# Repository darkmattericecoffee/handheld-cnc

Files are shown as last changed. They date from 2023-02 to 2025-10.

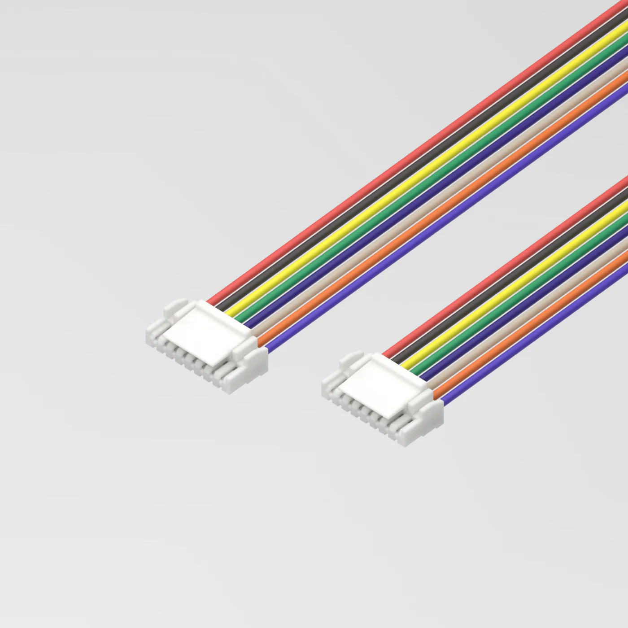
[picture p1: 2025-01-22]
cad/cha/sensor_ETH_20_CAT5/resources/jst_gh_8pin_v2.webp

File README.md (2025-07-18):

## Description
Compass is a DIY handheld CNC router designed to make CNC machining more accessible.

v1

Unlike traditional CNC machines that move a cutting tool within a fixed workspace, Compass relies on users to guide the device around the workpiece directly. It automatically adjusts the cutting tool to stay on the programmed design path, enabling a significantly smaller device footprint while still handling large-scale cuts.

This is all accomplished using optical flow mouse sensors to track the position of the device, as well as a lead screw driven gantry to adjust the tool. The brains are a Teensy 4.1 microcontroller.

## Getting Started
This repo contains all of the source to build a Handheld CNC Router: the firmware, CAD files for 3D printing/manufacturing, BOM, and cable diagrams.

### Navigation
Internal
- [main](main/) - main firmware (written for [PlatformIO](https://docs.platformio.org/en/latest/core/quickstart.html) usage)
- [cad](cad/) - custom hardware (3D prints, laser cut sheet metal, cable harnesses)
- [pcb](pcb/) - printed circuit board designs for motherboard and sensors
- [dev](dev/) - development folder for debugging and testing

External
- [BOM](https://docs.google.com/spreadsheets/d/12QS1CGSAB-lqKIOotCXDaXmJv9cjfRvVEAgQbRd7MnY/edit?usp=sharing)
- [Assembly Instructions](https://drive.google.com/drive/folders/1fIALrTWUbJRqTl93RGrUaR8dMfO7AI_g?usp=sharing)

## Disclaimer
This project is a work-in-progress. Development is rapidly occurring, so design files and firmware may change.

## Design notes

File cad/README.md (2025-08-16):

# Manufacturing BOM
Print all parts at 40% infill or higher. 

## 3D Printed Parts (PLA, unless stated otherwise)
- (2x) baseStage.stl
- (1x) baseStagePlug.stl
- (2x) cableClip.stl
- (1x) displayRing.stl
	- *_ae* if using AliExpress display
	- *_ws* if using Amazon Waveshare display
- (1x) frameUILeft.stl
- (1x) frameUIRight.stl
- (2x) handle.stl
- (1x) idlerMountLeft.stl
- (1x) idlerMountRight.stl
- (1x) mainFrame.stl
- (1x) motherEnclosure.stl
- (4x) PMW3360-sled.stl *(print at 0.1mm or 0.2mm layer height)*
- (1x) shieldSeperator.stl
- (3x) spacer_enclosure.stl
- (4x) springMount.stl *(print at 0.1mm or 0.2mm layer height)*
- (1x) stepperMountLeft.stl
- (1x) stepperMountRight.stl
- (1x) stepperMountZ.stl
- (2x) tensionPlug.stl
- (1x) vacMount.stl
- (1x) xStagePlate.stl
- (1x) yStagePlate.stl
- (1x) zCarriage.stl
- (1x) zKnob.stl
### Tool Mounts (PLA)
- 65mm tool mount (Makita RT0701C or any Makita router clone)
	- (2x) routerMount_65.stl
- 69mm tool mount (DeWalt 611) - *untested*
	- (2x) routerMount_69.stl
- Pen mounts (for testing)
	- (1x) penMount_65.stl
	- (1x) penMount_pm-65.stl
		- pen mount made for a Paper Mate flair tip pen
		- also randomly works for a Uniball rollerball
	- (1x) penMount_flange-pm-65.stl
		- same as above, but with a flange for easier alignment
### Jigs (PLA)
- (1x) encoderJig.stl
- (1x) beltShim.stl
- (1x) sensorJig.stl

## Aluminum Sheet Metal (6061)
- (1x) basePlate.dxf - 6mm (1/4" also works)
- (1x) facePlate.dxf - 1/16"
	- Note: this can be made in wood or acrylic too (1/8" should be fine) since it's not structural.
	- It can also be 3D printed or made using a PCB (see PCB folder...)

## Cable Harnesses
- (2x) sensorWire_ETH_20_CAT5
- (2x) sensorWire_ETH_40_CAT5

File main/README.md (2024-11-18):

## Debugging
To produce a debug logFile to use with `debugViewer.ipynb`, make sure the variable `outputMode` in your firmware is set to `1`. Then run the following code in a *platformIO terminal*:
```
pio device monitor > /logFiles/logFile_XX.txt
```

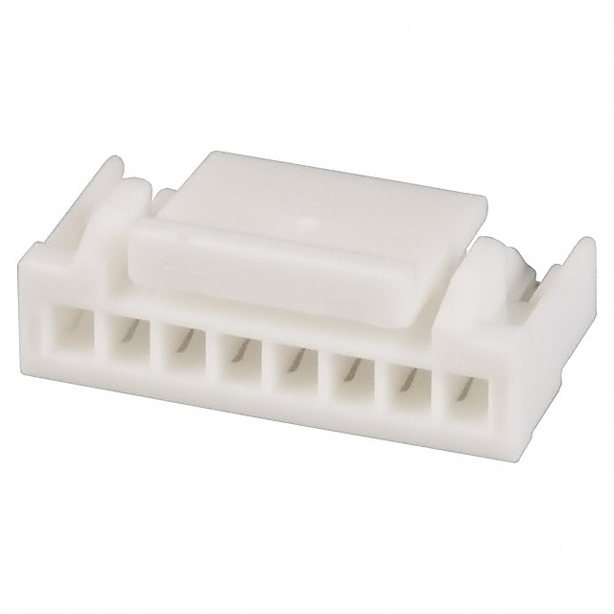
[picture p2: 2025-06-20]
cad/cha/sensor_ETH_20_CAT5/resources/GH-8.jpg

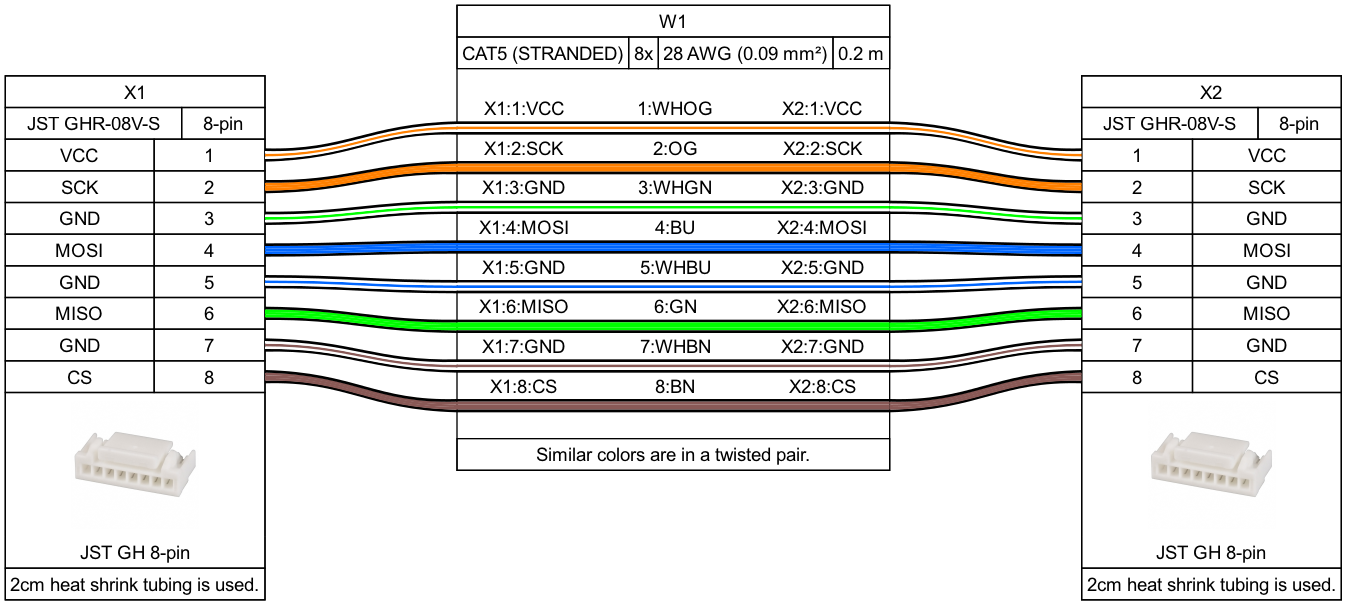
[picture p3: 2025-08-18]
cad/cha/sensor_ETH_20_CAT5/sensor_ETH_20_CAT5.png

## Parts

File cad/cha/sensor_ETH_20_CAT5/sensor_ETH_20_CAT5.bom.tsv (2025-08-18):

Id | Description | Qty | Unit | Designators
1 | Cable, CAT5 (STRANDED), 8 x 28 AWG | 0.2 | m | W1
2 | Connector, JST GHR-08V-S, 8 pins | 2 |  | X1, X2

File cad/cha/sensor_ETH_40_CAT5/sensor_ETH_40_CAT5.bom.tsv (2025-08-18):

Id | Description | Qty | Unit | Designators
1 | Cable, CAT5 (STRANDED), 8 x 28 AWG | 0.4 | m | W1
2 | Connector, JST GHR-08V-S, 8 pins | 2 |  | X1, X2

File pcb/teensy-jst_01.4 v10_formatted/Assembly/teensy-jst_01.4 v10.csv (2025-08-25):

Qty | Value | Device | Package | Parts | Description | AVAILABILITY | CATEGORY | CHECK_PRICES | COPYRIGHT | DESCRIPTION | MANUFACTURER | MANUFACTURER_PART_NUMBER | MF | MFR_NAME | MP | MPN | OPERATING_TEMP | PACKAGE | PART_STATUS | POPULARITY | PRICE | PROD_ID | RATING | ROHS_COMPLIANT | SERIES | SF_SKU | SNAPEDA_LINK | SPICEPREFIX | SUB-CATEGORY | THERMALLOSS | TOLERANCE | TYPE | VALUE | VOLTAGE_RATING
2 |  | CONN_025MM | SCREWTERMINAL-5MM-2 | 5V_IN, 24V_IN | Multi connection point. Often used as Generic Header-pin footprint for 0.1 inch spaced/style header connections |  |  |  |  |  |  |  |  |  |  |  |  |  |  |  |  |  |  |  |  | PRT-08432
11 |  |  | 1X08 | DISPLAY, HX1, HX2, HY1, HY2, HZ1, HZ2, SEN0-S, SEN1-S, SEN2-S, SEN3-S | Multi connection point. Often used as Generic Header-pin footprint for 0.1 inch spaced/style header connections |  |  |  |  |  |  |  |  |  |  |  |  |  |  |  |  | CONN-08438
1 |  |  | 1X10 | J5 | Multi connection point. Often used as Generic Header-pin footprint for 0.1 inch spaced/style header connections |  |  |  |  |  |  |  |  |  |  |  |  |  |  |  |  | CONN-11563
6 |  | CONN_24 | 1X24 | T1, T2, T3, T4, T5, T6 | Multi connection point. Often used as Generic Header-pin footprint for 0.1 inch spaced/style header connections
1 | 0R | R-US_CHIP-0603(1608-METRIC) | RESC1608X60 | R3 | Resistor Fixed - ANSI |  | Resistor |  |  |  |  |  |  |  |  |  |  |  |  |  |  |  |  |  |  |  |  |  | Fixed
9 | 100R | R-US_CHIP-0603(1608-METRIC) | RESC1608X60 | R4, R5, R15, R16, R17, R18, R20, R21, R22 | Resistor Fixed - ANSI |  | Resistor |  |  |  |  |  |  |  |  |  |  |  |  |  |  |  |  |  |  |  |  |  | Fixed
1 | 100k | R-US_CHIP-0402(1005-METRIC) | RESC1005X40 | R23 | Resistor Fixed - ANSI |  | Resistor |  |  |  |  |  |  |  |  |  |  |  |  |  |  |  |  |  |  |  |  |  | Fixed
5 | 100nF | C_CHIP-0402(1005-METRIC) | CAPC1005X60 | C9, C14, C15, C16, C17 | Capacitor - Generic |  | Capacitor
3 | 100nF | C_CHIP-0603(1608-METRIC) | CAPC1608X85 | C3, C4, C28 | Capacitor - Generic |  | Capacitor
10 | 100pF | C_CHIP-0402(1005-METRIC) | CAPC1005X60 | C18, C19, C20, C21, C22, C23, C24, C25, C26, C27 | Capacitor - Generic |  | Capacitor
4 | 100uF/50V | CPOL-USD | PANASONIC_D | C1, C2, C12, C13 | POLARIZED CAPACITOR, American symbol |  |  |  |  |  |  |  |  |  |  |  |  |  |  | 7 |  |  |  |  |  |  |  | C
11 | 10k | R-US_CHIP-0603(1608-METRIC) | RESC1608X60 | R1, R2, R6, R7, R9, R10, R11, R12, R13, R14, R27 | Resistor Fixed - ANSI |  | Resistor |  |  |  |  |  |  |  |  |  |  |  |  |  |  |  |  |  |  |  |  |  | Fixed
1 | 10uH | L-USMWSA0503S-100MT | MWSA0503S-100MT | L1 | INDUCTOR, American symbol
1 | 13k | R-US_CHIP-0603(1608-METRIC) | RESC1608X60 | R24 | Resistor Fixed - ANSI |  | Resistor |  |  |  |  |  |  |  |  |  |  |  |  |  |  |  |  |  |  |  |  |  | Fixed
1 | 1k | R-US_CHIP-0603(1608-METRIC) | RESC1608X60 | R8 | Resistor Fixed - ANSI |  | Resistor |  |  |  |  |  |  |  |  |  |  |  |  |  |  |  |  |  |  |  |  |  | Fixed
2 | 2.2uF | C_CHIP-0603(1608-METRIC) | CAPC1608X85 | C5, C6 | Capacitor - Generic |  | Capacitor
1 | 270k | R-US_CHIP-0402(1005-METRIC) | RESC1005X40 | R26 | Resistor Fixed - ANSI |  | Resistor |  |  |  |  |  |  |  |  |  |  |  |  |  |  |  |  |  |  |  |  |  | Fixed
1 | 39pF | C_CHIP-0402(1005-METRIC) | CAPC1005X60 | C8 | Capacitor - Generic |  | Capacitor
2 | 455-1750-1-ND | CONN_03 | 1X03 | G1, V5 | Multi connection point. Often used as Generic Header-pin footprint for 0.1 inch spaced/style header connections |  |  |  |  |  |  |  |  |  |  |  |  |  |  |  |  | XXX-00000 |  |  |  |  |  |  |  |  |  |  | 455-1750-1-ND
2 | 47uF | C_CHIP-0805(2012-METRIC) | CAPC2012X110 | C10, C11 | Capacitor - Generic |  | Capacitor
1 | 51k | R-US_CHIP-0603(1608-METRIC) | RESC1608X60 | R25 | Resistor Fixed - ANSI |  | Resistor |  |  |  |  |  |  |  |  |  |  |  |  |  |  |  |  |  |  |  |  |  | Fixed
1 | 6.8nF | C_CHIP-0603(1608-METRIC) | CAPC1608X85 | C7 | Capacitor - Generic |  | Capacitor
1 | B560C-13-FSMC_DIO-L | B560C-13-FSMC_DIO-L | SMC_DIO-L | CR1 |  |  |  |  | Copyright (C) 2024 Ultra Librarian. All rights reserved. |  |  | B560C-13-F |  | Diodes Inc
4 | BM08B-GHS-TBT(LF)(SN)(N) | BM08B-GHS-TBT(LF)(SN)(N) | JST_BM08B-GHS-TBT(LF)(SN)(N) | SEN0, SEN1, SEN2, SEN3 | Conn Header Gh Top 8pos 1.25mm Check availability | In Stock |  | https://www.snapeda.com/parts/BM08B-GHS-TBT(LF)(SN)(N)/JST+Sales+America+Inc./view-part/?ref=eda |  | Connector Header Surface Mount 8 position 0.049 (1.25mm) |  |  | JST Sales |  | BM08B-GHS-TBT(LF)(SN)(N) |  |  | None |  |  | None |  |  |  |  |  | https://www.snapeda.com/parts/BM08B-GHS-TBT(LF)(SN)(N)/JST+Sales+America+Inc./view-part/?ref=snap
3 | HX25418-4A | HX25418-4A | HX25418-4A | X_OUT, Y_OUT, Z_OUT
1 | TPS54360DDARDDA8_3P1X2P4_TEX | TPS54360DDARDDA8_3P1X2P4_TEX | DDA8_3P1X2P4_TEX | U1 |  |  |  |  | Copyright (C) 2024 Ultra Librarian. All rights reserved. |  |  | TPS54360DDAR |  | Texas Instruments

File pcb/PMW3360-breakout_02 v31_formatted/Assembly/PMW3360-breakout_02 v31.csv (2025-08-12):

Qty | Value | Device | Package | Parts | Description | AVAILABILITY | CATEGORY | CHECK_PRICES | COPYRIGHT | DESCRIPTION | MANUFACTURER | MANUFACTURER_PART_NUMBER | MF | MFR_NAME | MP | MPN | OPERATING_TEMP | PACKAGE | PART_STATUS | POPULARITY | PRICE | PROD_ID | ROHS_COMPLIANT | SERIES | SNAPEDA_LINK | SPICEPREFIX | SUB-CATEGORY | THERMALLOSS | TYPE | VOLTAGE_RATING
1 |  | CONN_02 | 1X02 | J2 | Multi connection point. Often used as Generic Header-pin footprint for 0.1 inch spaced/style header connections
1 |  |  | 1X08 | J1 | Multi connection point. Often used as Generic Header-pin footprint for 0.1 inch spaced/style header connections |  |  |  |  |  |  |  |  |  |  |  |  |  |  |  |  | CONN-08438
1 | 0R | R-US_R0402 | R0402 | R5 | RESISTOR, American symbol |  |  |  |  |  |  |  |  |  |  |  |  |  |  | 34 |  |  |  |  |  | R
1 | 100 | R-US_R0402 | R0402 | R4 | RESISTOR, American symbol |  |  |  |  |  |  |  |  |  |  |  |  |  |  | 34 |  |  |  |  |  | R
4 | 100nF | C_CHIP-0402(1005-METRIC) | CAPC1005X60 | C2, C4, C8, C10 | Capacitor - Generic |  | Capacitor
1 | 100pF | C-EUC0402K | C0402K | C11 | CAPACITOR, European symbol |  |  |  |  |  |  |  |  |  |  |  |  |  |  | 15 |  |  |  |  |  | C
2 | 10k | R-US_R0402 | R0402 | R1, R3 | RESISTOR, American symbol |  |  |  |  |  |  |  |  |  |  |  |  |  |  | 34 |  |  |  |  |  | R
3 | 10uF | C_CHIP-0402(1005-METRIC) | CAPC1005X60 | C3, C7, C9 | Capacitor - Generic |  | Capacitor
2 | 1uF | C_CHIP-0402(1005-METRIC) | CAPC1005X60 | C5, C6 | Capacitor - Generic |  | Capacitor
1 | 39 | R-US_R0402 | R0402 | R2 | RESISTOR, American symbol |  |  |  |  |  |  |  |  |  |  |  |  |  |  | 34 |  |  |  |  |  | R
1 | 4.7uF/10V | C_CHIP-0603(1608-METRIC) | CAPC1608X85 | C1 | Capacitor - Generic |  | Capacitor
1 | BM08B-GHS-TBT(LF)(SN)(N) | BM08B-GHS-TBT(LF)(SN)(N) | JST_BM08B-GHS-TBT(LF)(SN)(N) | P1 | Conn Header Gh Top 8pos 1.25mm Check availability | In Stock |  | https://www.snapeda.com/parts/BM08B-GHS-TBT(LF)(SN)(N)/JST+Sales+America+Inc./view-part/?ref=eda |  | Connector Header Surface Mount 8 position 0.049 (1.25mm) |  |  | JST Sales |  | BM08B-GHS-TBT(LF)(SN)(N) |  |  | None |  |  | None |  |  |  | https://www.snapeda.com/parts/BM08B-GHS-TBT(LF)(SN)(N)/JST+Sales+America+Inc./view-part/?ref=snap
1 | PMW3360PMW3360-LM19 | PMW3360PMW3360-LM19 | PMW3360 | PMW3360
1 | TLV70019DDCRDDC5-L | TLV70019DDCRDDC5-L | DDC5-L | U2 |  |  |  |  | Copyright (C) 2024 Ultra Librarian. All rights reserved. |  |  | TLV70019DDCR |  | Texas Instruments

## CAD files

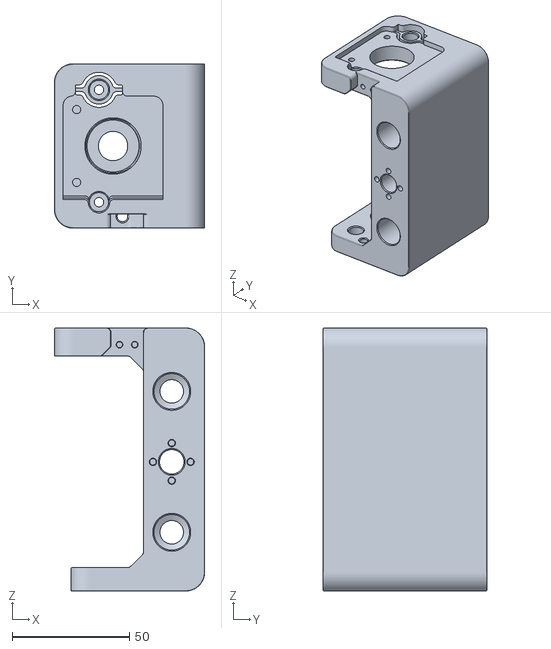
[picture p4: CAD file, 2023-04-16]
CAD/Main Assembly/latest/mainFrame.stl
64.0 x 70.0 x 112.0

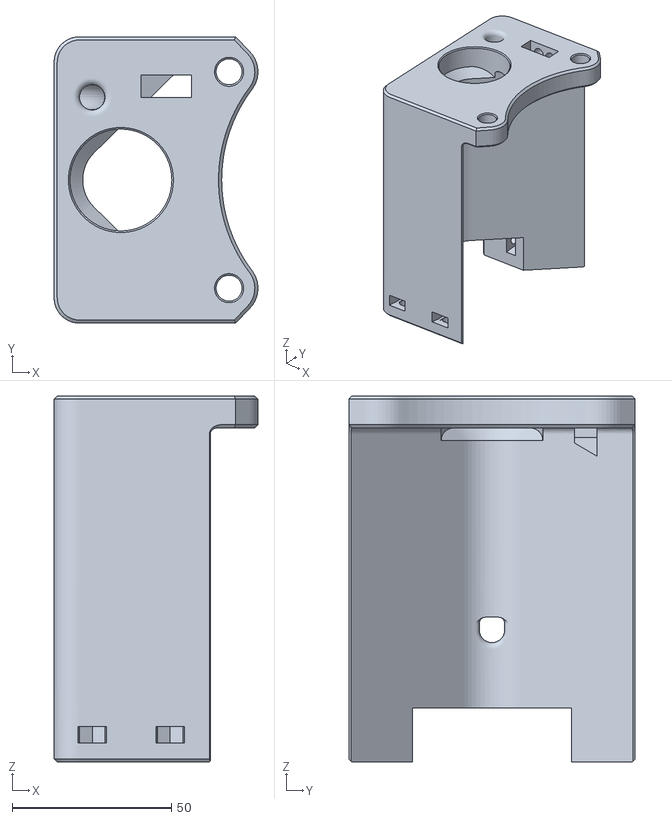
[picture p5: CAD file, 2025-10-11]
cad/fdm/mainFrame.stl
64.1 x 90.0 x 115.0

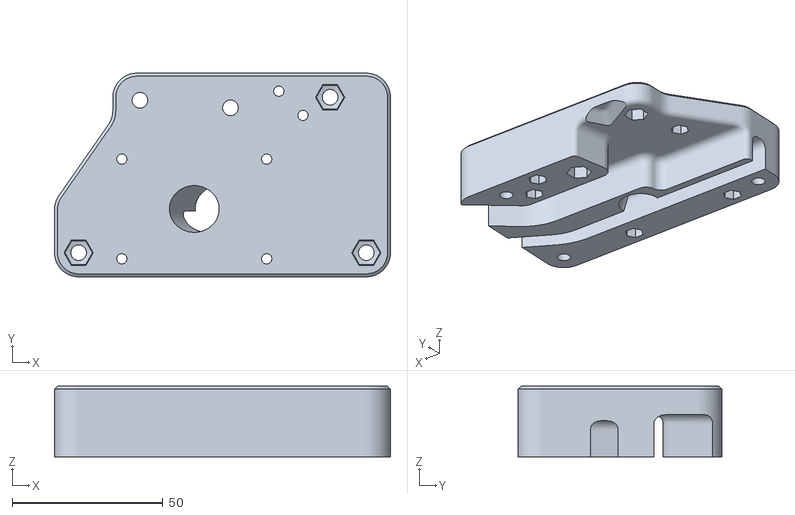
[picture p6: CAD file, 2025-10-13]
cad/fdm/idlerMountLeft.stl
111.3 x 67.5 x 23.5

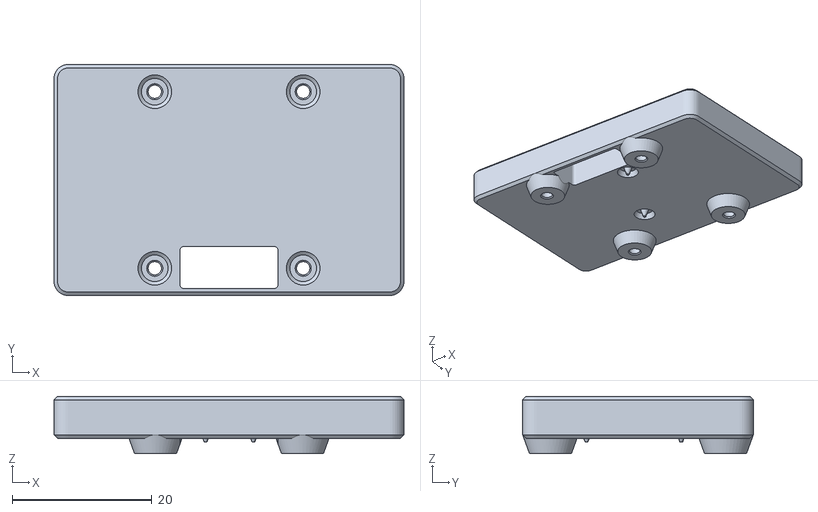
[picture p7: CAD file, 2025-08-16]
cad/fdm/jigs/sensor-jig.stl
50.0 x 33.0 x 8.20

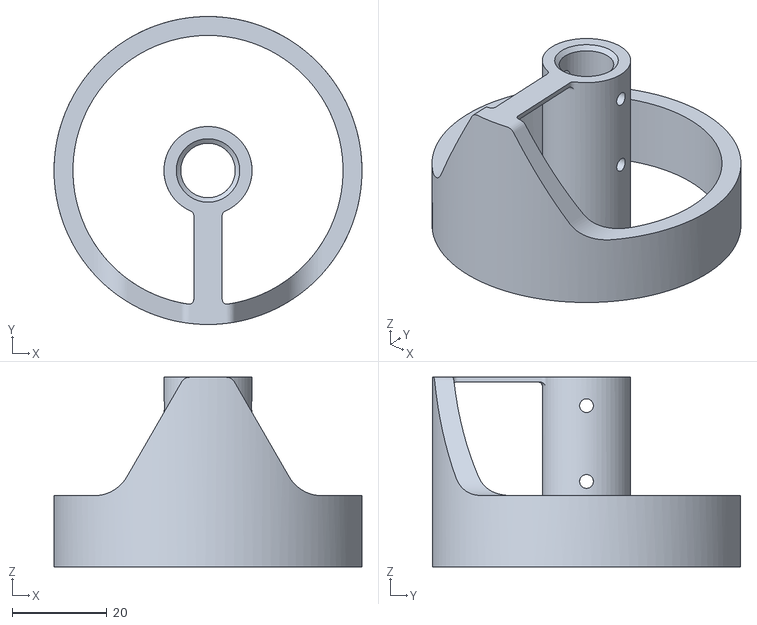
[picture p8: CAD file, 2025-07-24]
cad/fdm/tool-mounts/penMount_65.stl
65.0 x 65.0 x 40.0

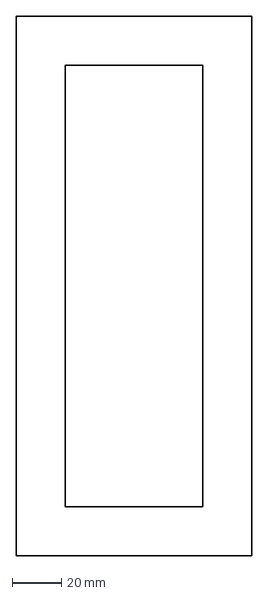
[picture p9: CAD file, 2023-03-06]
CAD/Sensor Calibration/frameRail.dxf
96.0 x 220.0 mm

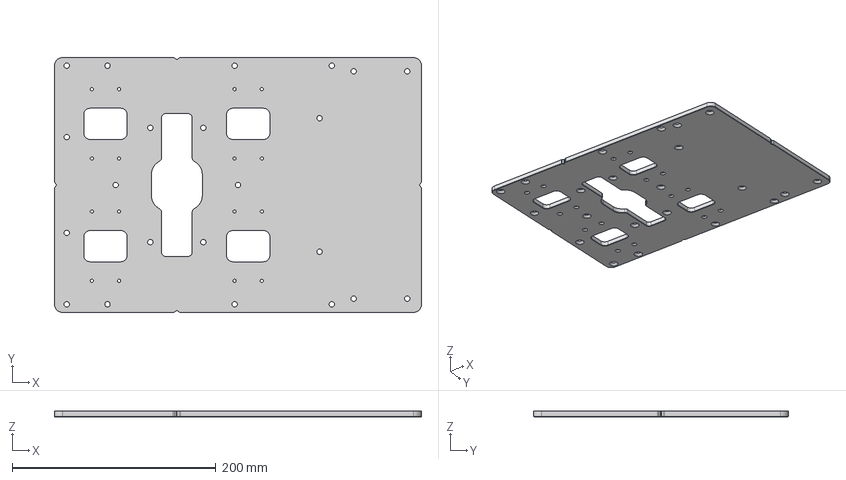
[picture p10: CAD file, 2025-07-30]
cad/shm/basePlate.step
360.0 x 250.0 x 6.00 mm

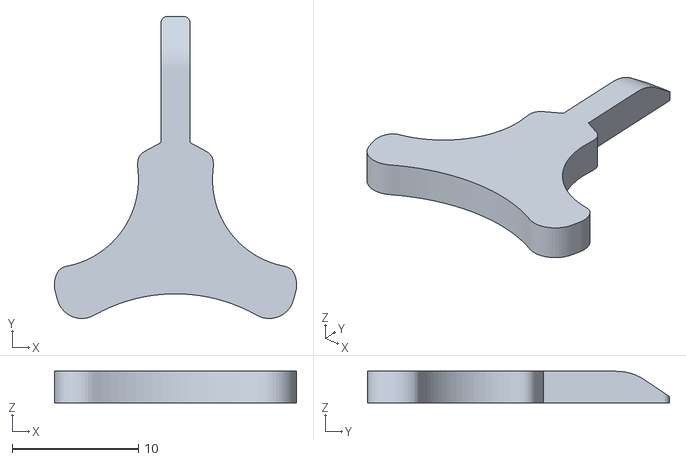
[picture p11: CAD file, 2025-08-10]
cad/fdm/jigs/beltShim.stl
19.2 x 24.0 x 2.50

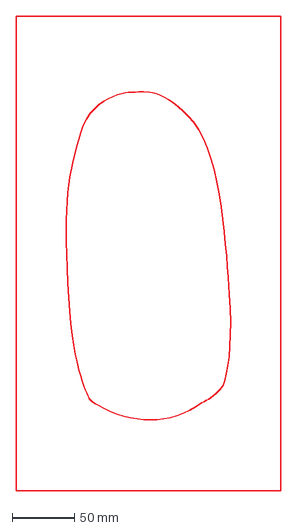
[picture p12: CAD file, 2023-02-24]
CAD/Sensor Calibration/mousefinal.dxf
212.6 x 381.0 mm

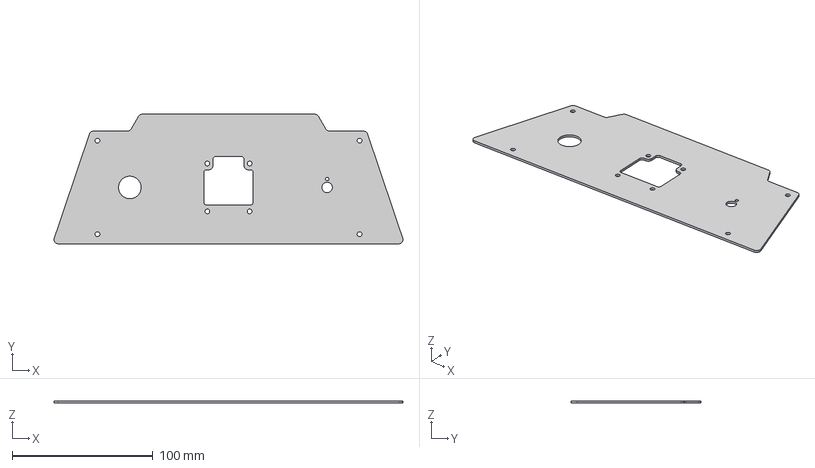
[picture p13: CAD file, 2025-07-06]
cad/shm/facePlate.step
247.6 x 92.0 x 1.59 mm

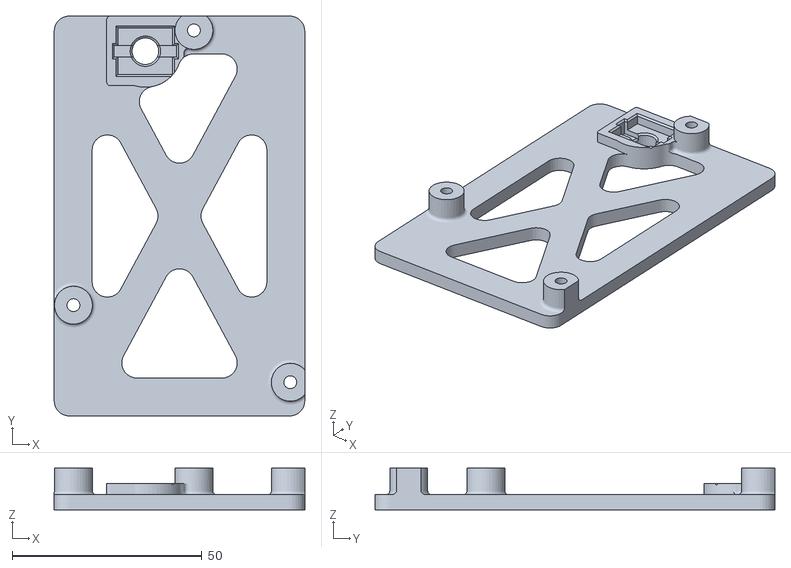
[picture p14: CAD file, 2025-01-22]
cad/fdm/jigs/encoderJig.stl
66.0 x 105.4 x 11.0

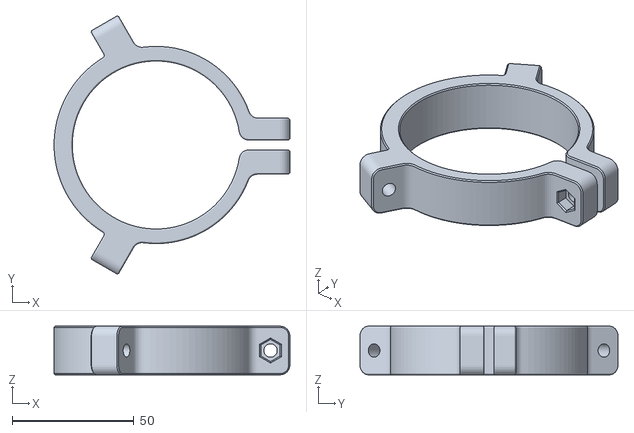
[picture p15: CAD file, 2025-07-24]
cad/fdm/tool-mounts/routerMount_69.stl
96.9 x 106.0 x 20.0

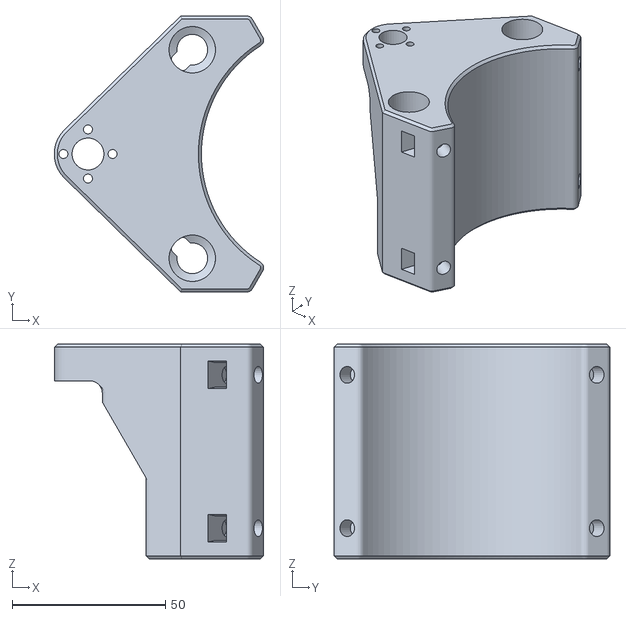
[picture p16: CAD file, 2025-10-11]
cad/fdm/zCarriage.stl
68.3 x 90.0 x 70.0

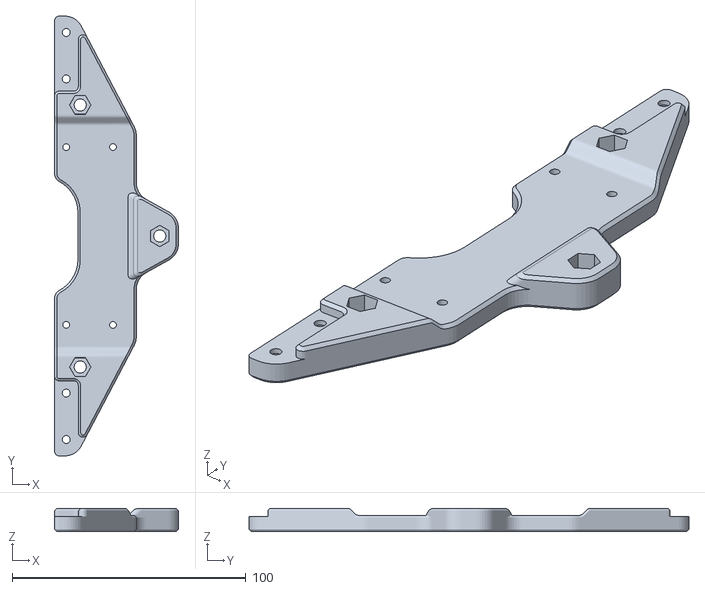
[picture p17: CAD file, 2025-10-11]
cad/fdm/baseStage.stl
53.0 x 188.0 x 10.0

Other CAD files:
cad/fdm/idlerMountLeftRight.stl
cad/fdm/tool-mounts/penMount_pm-65.stl
cad/fdm/tool-mounts/routerMount_65.stl
cad/fdm/tool-mounts/penMount_flange-pm-65.stl
cad/fdm/PMW3360-sled.stl
cad/fdm/baseStagePlug.stl
cad/fdm/cableClip.stl
cad/fdm/displayRing_01.stl
cad/fdm/frameUILeft.stl
cad/fdm/frameUIRight.stl
cad/fdm/handle.stl
cad/fdm/motherEnclosure.stl
cad/fdm/shieldSeparator.stl
cad/fdm/spacer_enclosure.stl
cad/fdm/springMount.stl
cad/fdm/stepperMountLeft.stl
cad/fdm/stepperMountRight.stl
cad/fdm/stepperMountZ.stl
cad/fdm/tensionPlug.stl
cad/fdm/vacMount.stl
cad/fdm/xStagePlate.stl
cad/fdm/yStagePlate.stl
cad/fdm/zKnob_01.stl
cad/shm/baseplate.dxf
cad/shm/facePlate.dxf

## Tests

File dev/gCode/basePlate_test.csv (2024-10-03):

x | y | z
214.729 | 66.016 | 15.24
214.729 | 66.016 | 5.08
214.729 | 66.016 | 0.635
214.729 | 66.016 | -7.366
214.729 | 78.016 | -7.366
214.721 | 78.335 | -7.366
214.698 | 78.654 | -7.366
214.66 | 78.971 | -7.366
214.607 | 79.286 | -7.366
214.539 | 79.599 | -7.366
214.457 | 79.907 | -7.366
214.359 | 80.211 | -7.366
214.248 | 80.511 | -7.366
214.122 | 80.804 | -7.366
213.982 | 81.092 | -7.366
213.829 | 81.372 | -7.366
213.663 | 81.645 | -7.366
213.484 | 81.91 | -7.366
213.292 | 82.165 | -7.366
213.089 | 82.412 | -7.366
212.874 | 82.648 | -7.366
212.648 | 82.874 | -7.366
212.412 | 83.089 | -7.366
212.165 | 83.292 | -7.366
211.91 | 83.484 | -7.366
211.645 | 83.663 | -7.366
211.372 | 83.829 | -7.366
211.092 | 83.982 | -7.366
210.804 | 84.122 | -7.366
210.511 | 84.248 | -7.366
210.211 | 84.359 | -7.366
209.907 | 84.457 | -7.366
209.599 | 84.539 | -7.366
209.286 | 84.607 | -7.366
208.971 | 84.66 | -7.366
208.654 | 84.698 | -7.366
208.335 | 84.721 | -7.366
208.016 | 84.729 | -7.366
174.016 | 84.729 | -7.366
173.697 | 84.721 | -7.366
173.378 | 84.698 | -7.366
173.061 | 84.66 | -7.366
172.746 | 84.607 | -7.366
172.433 | 84.539 | -7.366
172.125 | 84.457 | -7.366
171.821 | 84.359 | -7.366
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

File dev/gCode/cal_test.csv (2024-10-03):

x | y | z
101.099 | 102.876 | 15.24
101.099 | 102.876 | 5.08
101.099 | 102.876 | 0.635
101.099 | 102.876 | -9.016
101.414 | 103.108 | -9.016
101.433 | 103.122 | -9.016
102.166 | 103.645 | -9.016
102.187 | 103.66 | -9.016
102.928 | 104.171 | -9.016
102.946 | 104.183 | -9.016
103.694 | 104.684 | -9.016
103.716 | 104.699 | -9.016
104.472 | 105.187 | -9.016
104.492 | 105.199 | -9.016
105.257 | 105.677 | -9.016
105.278 | 105.691 | -9.016
106.051 | 106.157 | -9.016
106.073 | 106.169 | -9.016
106.854 | 106.623 | -9.016
106.875 | 106.635 | -9.016
107.664 | 107.078 | -9.016
107.686 | 107.09 | -9.016
108.483 | 107.521 | -9.016
108.507 | 107.534 | -9.016
109.382 | 107.988 | -9.016
109.409 | 108.002 | -9.016
110.292 | 108.439 | -9.016
110.319 | 108.452 | -9.016
111.21 | 108.872 | -9.016
111.24 | 108.886 | -9.016
112.139 | 109.287 | -9.016
112.168 | 109.299 | -9.016
113.074 | 109.682 | -9.016
113.107 | 109.696 | -9.016
114.022 | 110.059 | -9.016
114.054 | 110.071 | -9.016
114.977 | 110.414 | -9.016
115.01 | 110.426 | -9.016
115.942 | 110.749 | -9.016
115.976 | 110.76 | -9.016
116.913 | 111.061 | -9.016
116.95 | 111.073 | -9.016
117.893 | 111.351 | -9.016
117.929 | 111.361 | -9.016
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

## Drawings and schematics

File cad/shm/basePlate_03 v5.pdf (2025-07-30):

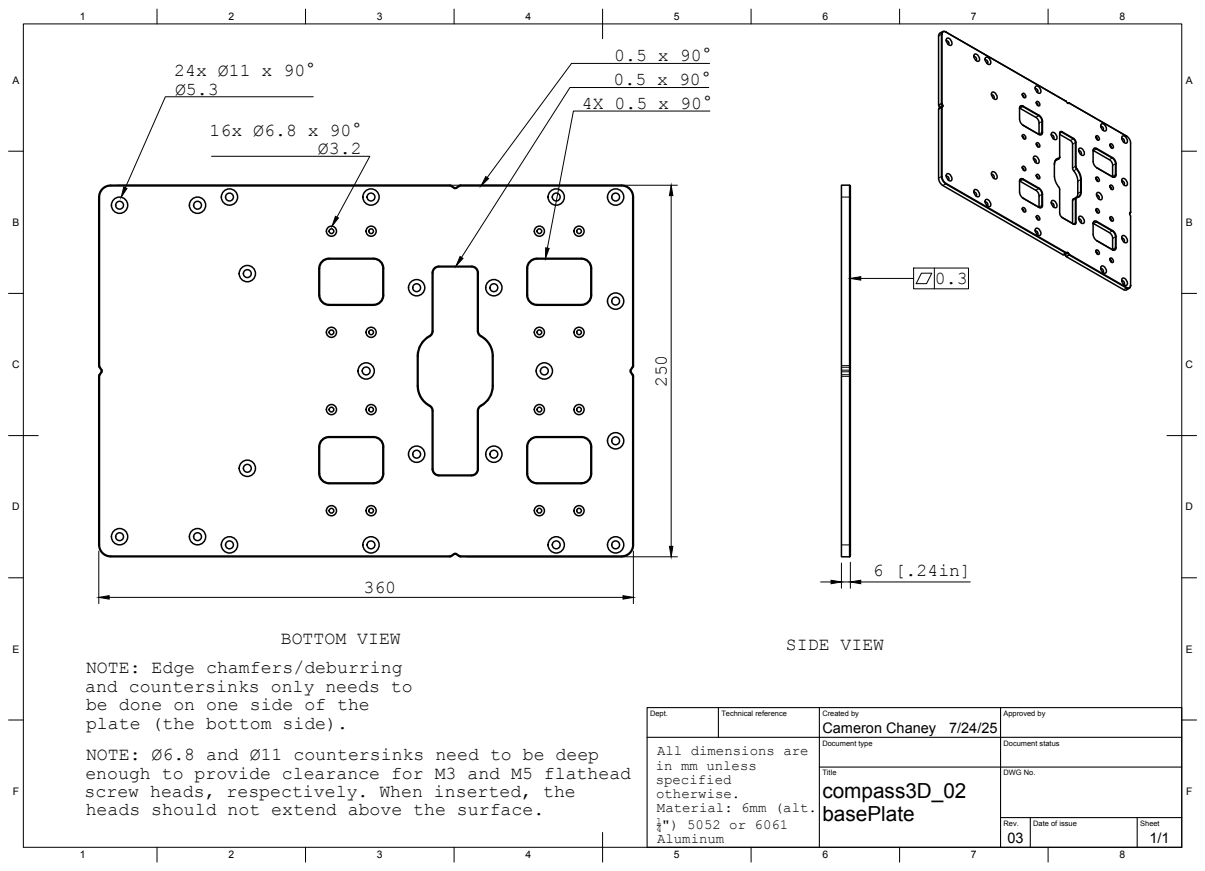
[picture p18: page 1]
Title; DWG No.; Rev.; Date of issue; Sheet; BOTTOM VIEW; SIDE VIEW

NOTE: Edge chamfers/deburring
and countersinks only needs to
be done on one side of the
plate (the bottom side).

Dept. | Technical reference | Created by Cameron Chaney 7/24/25 | Approved by

Document type | Document status

NOTE: Ø6.8 and Ø11 countersinks need to be deep
enough to provide clearance for M3 and M5 flathead
screw heads, respectively. When inserted, the
heads should not extend above the surface.

All dimensions are
in mm unless
specified
otherwise.
Material: 6mm (alt.
Aluminum

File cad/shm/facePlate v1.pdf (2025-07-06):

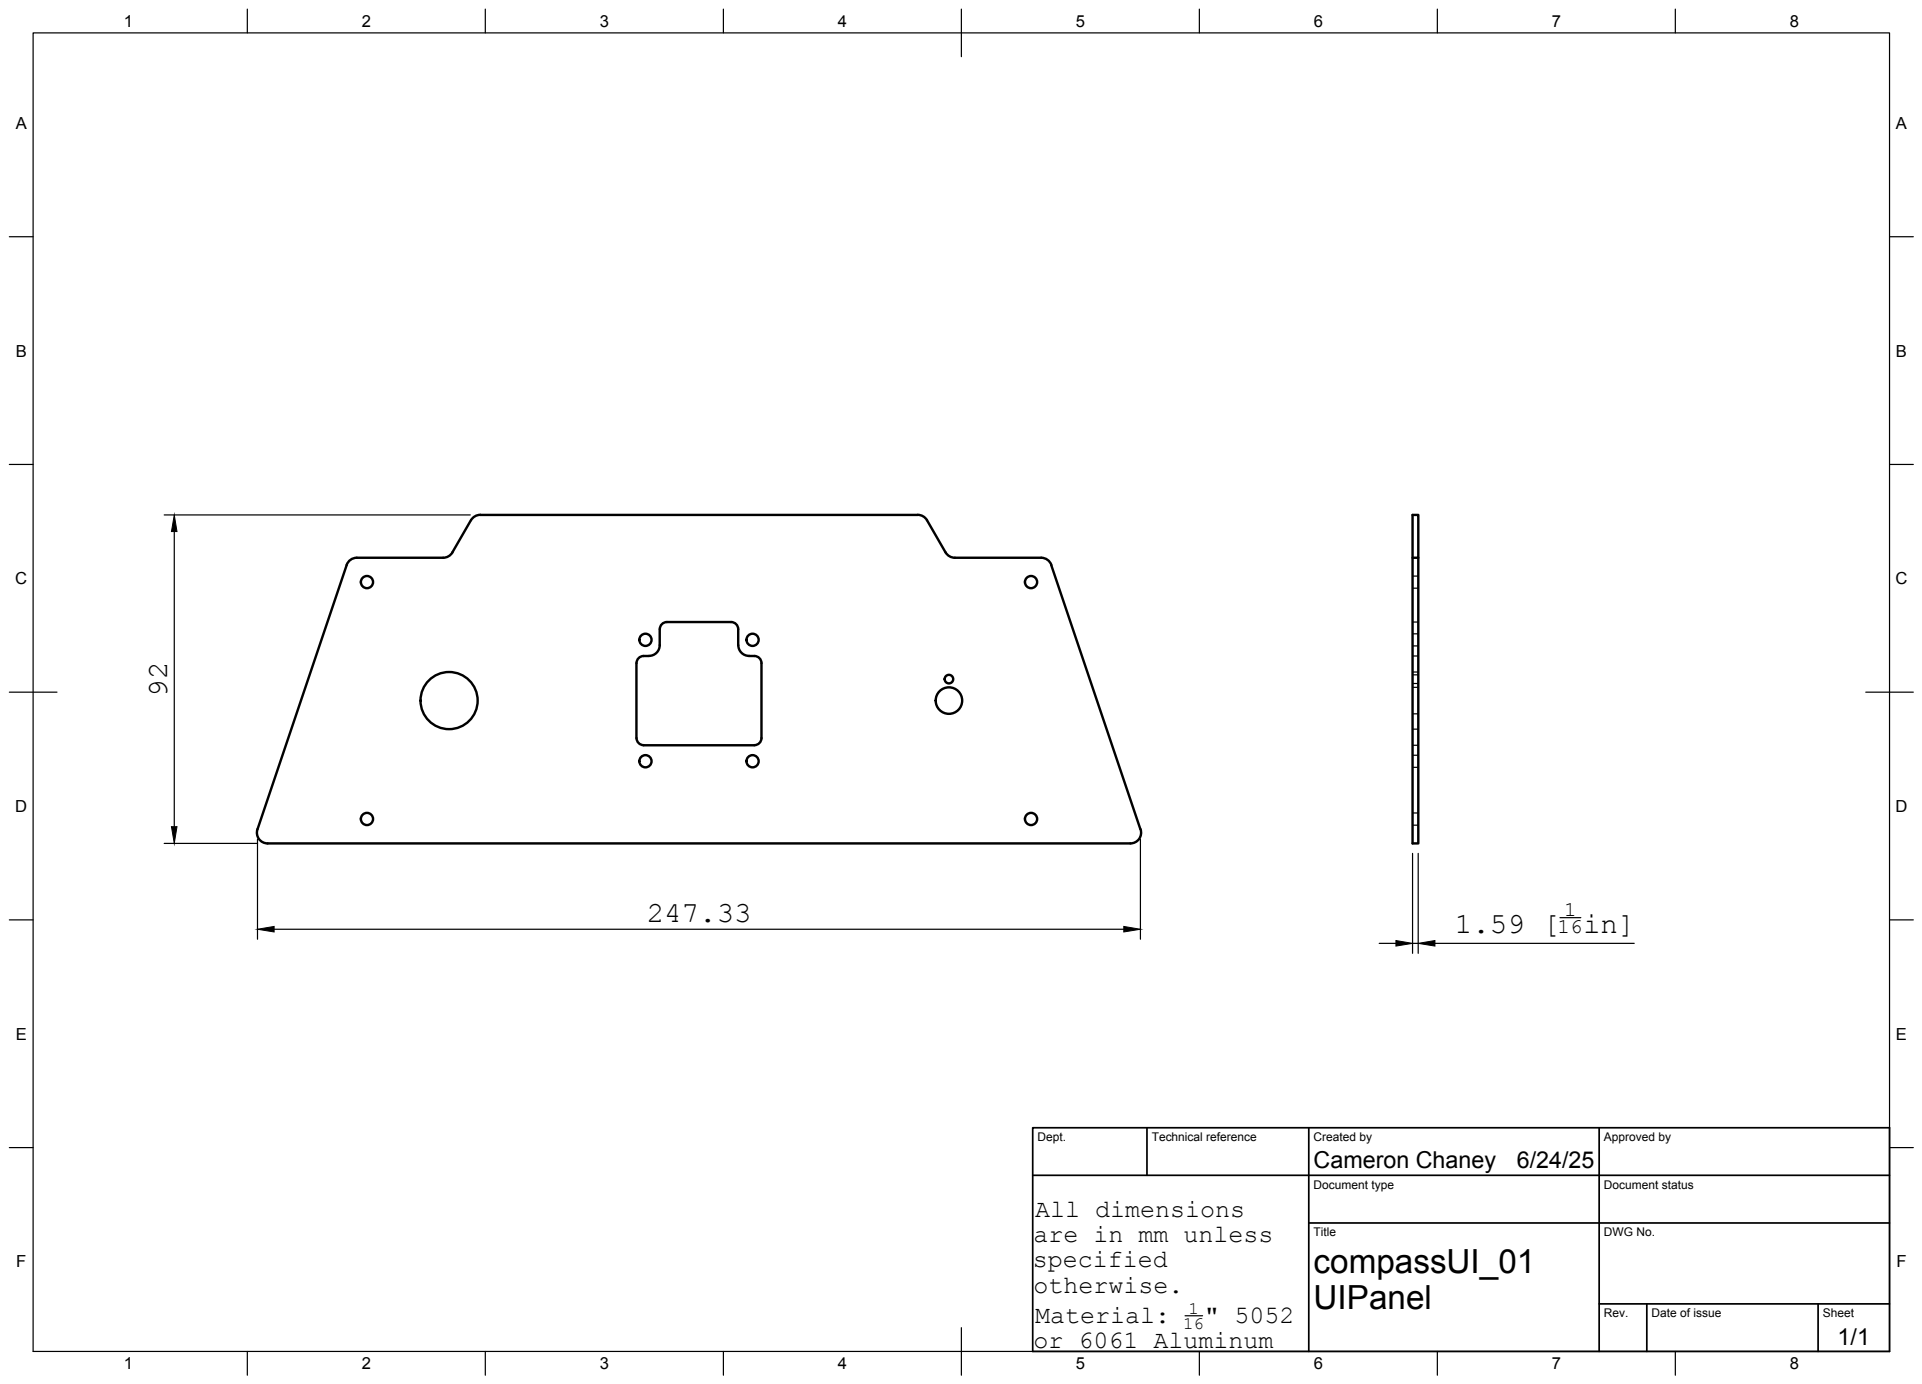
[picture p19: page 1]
Title; DWG No.; Rev.; Date of issue; Sheet

Dept. | Technical reference | Created by Cameron Chaney 6/24/25 | Approved by

Document type | Document status

All dimensions
are in mm unless
specified
otherwise.
Material: 1
or 6061 Aluminum

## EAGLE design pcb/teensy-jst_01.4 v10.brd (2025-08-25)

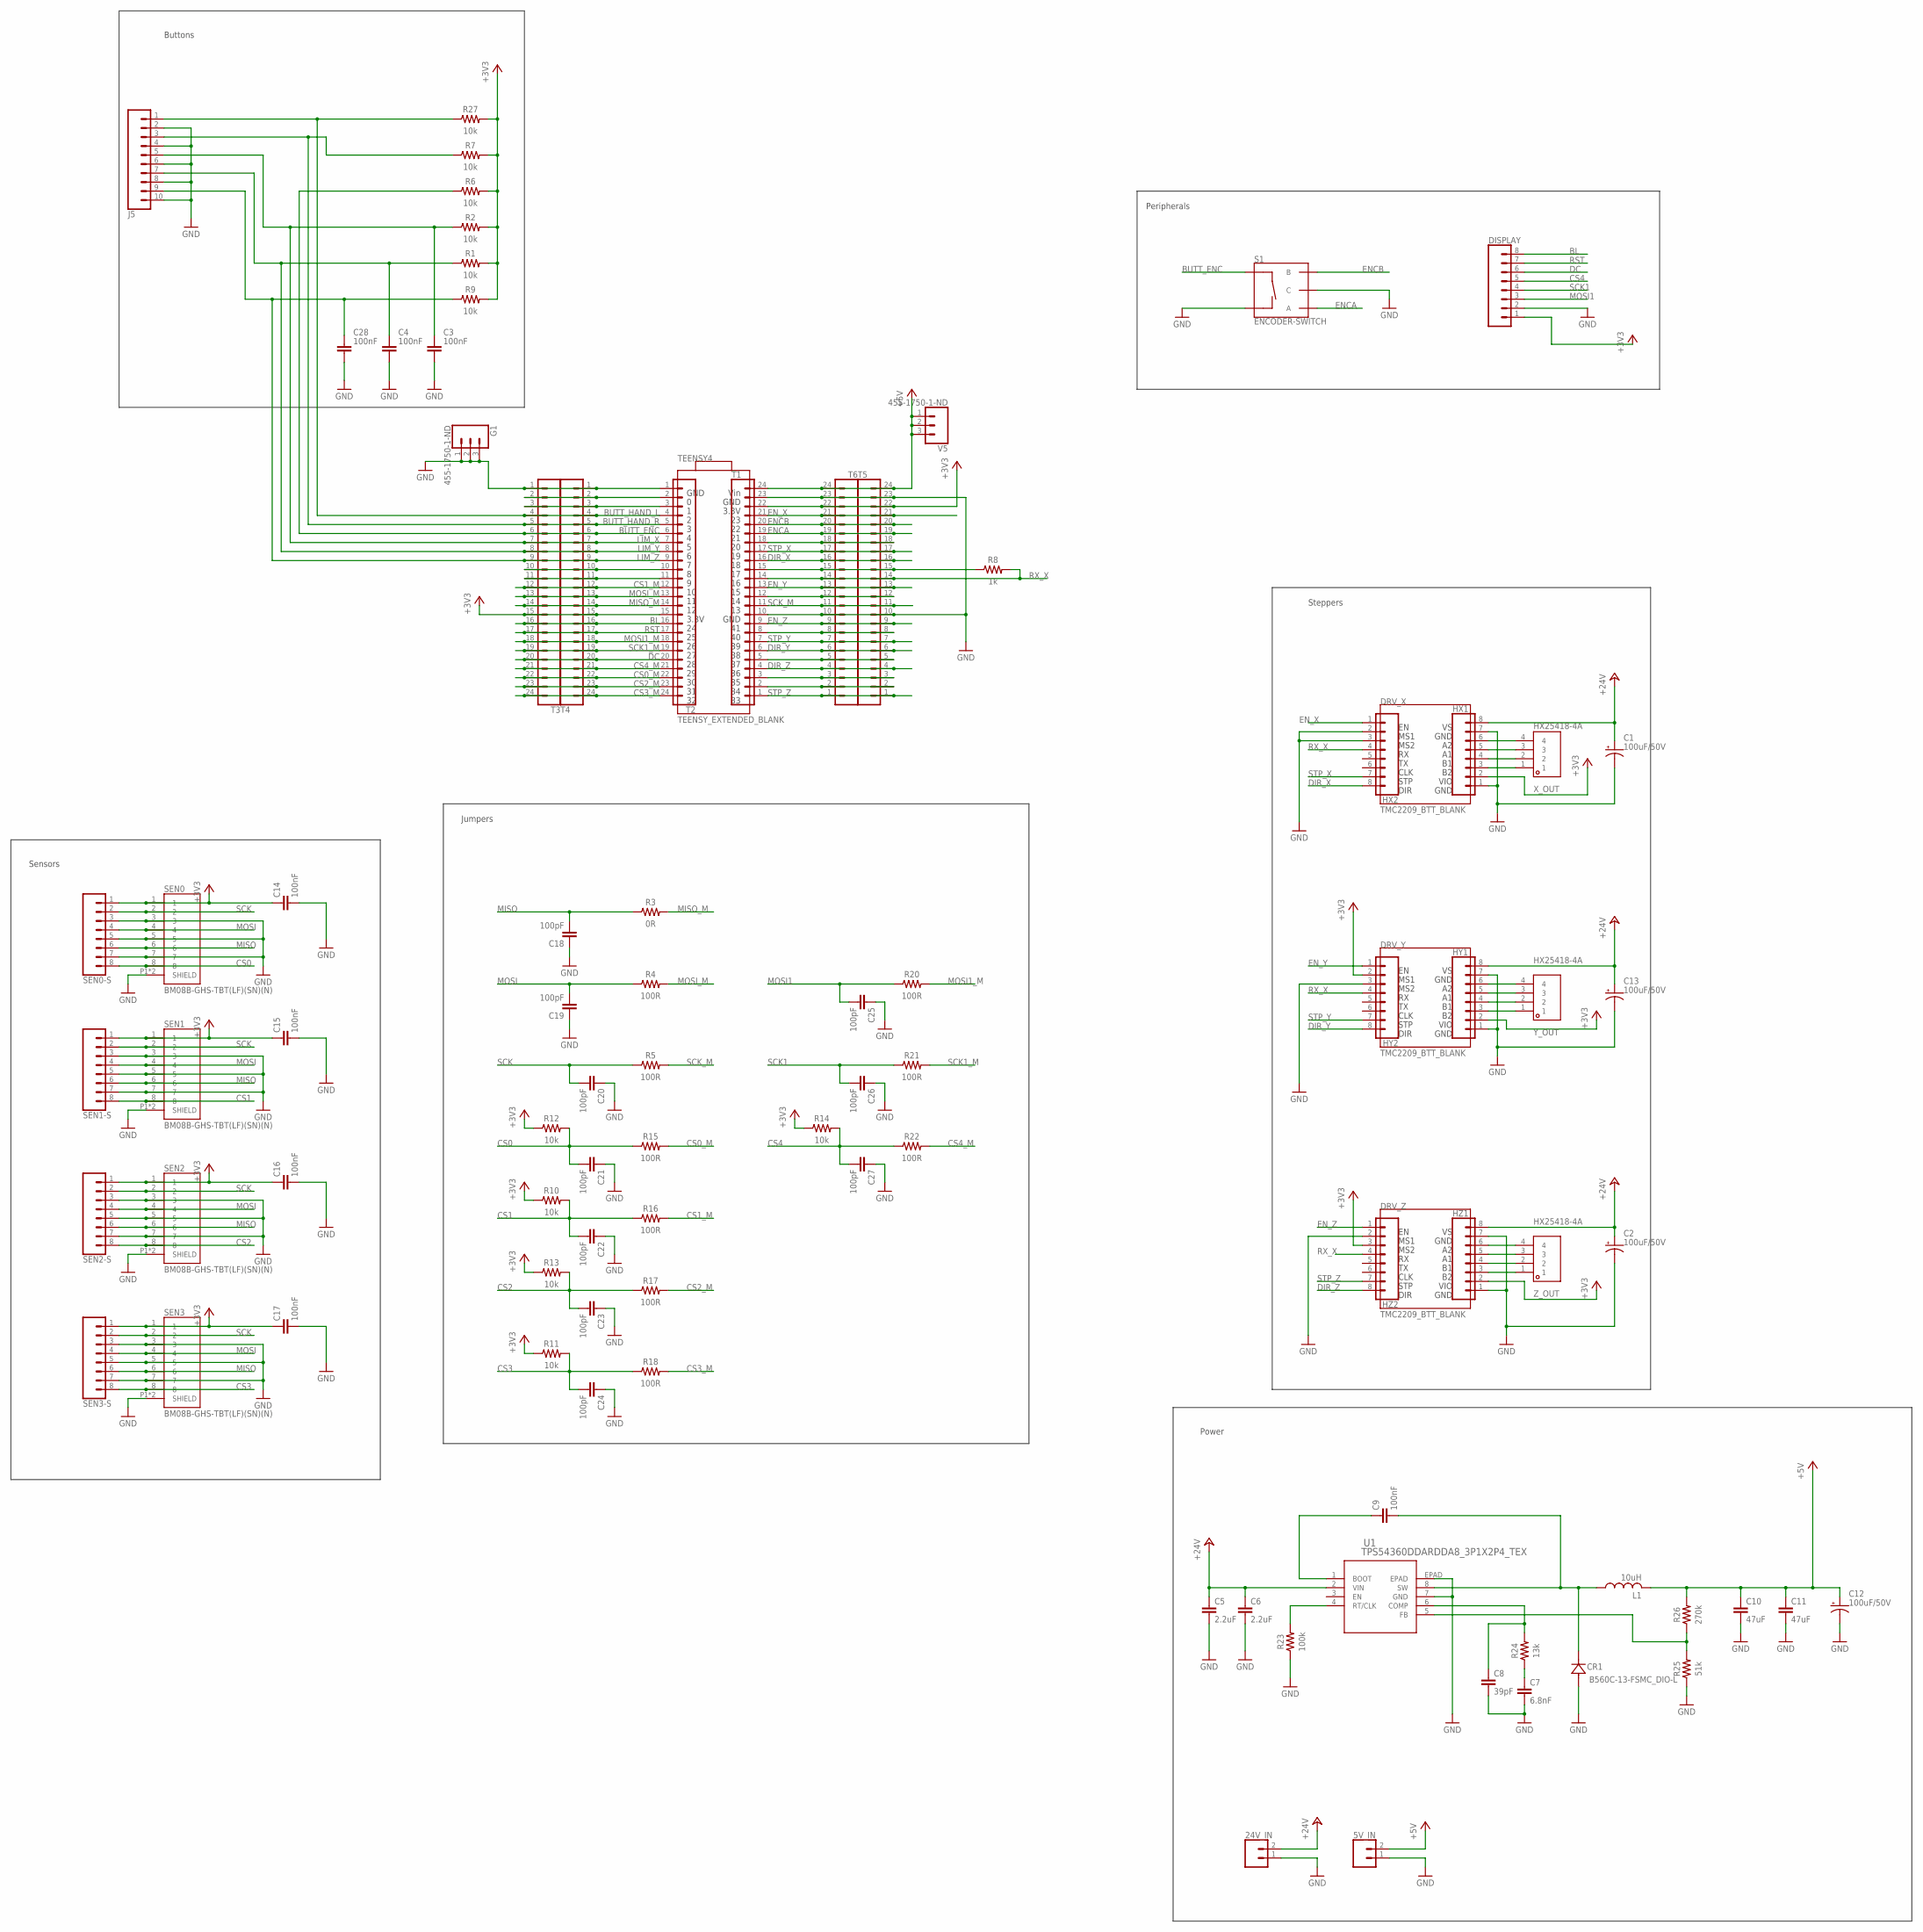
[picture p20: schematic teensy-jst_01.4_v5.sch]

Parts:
5V_IN, 24V_IN: CONN_025MM; SCREWTERMINAL-5MM-2
C1, C2, C12, C13: 100uF/50V; PANASONIC_D
C3, C4, C28: 100nF; C0603
C5, C6: 2.2uF; C0603
C7: 6.8nF; C0603
C8: 39pF; C0402
C9, C14, C15, C16, C17: 100nF; C0402
C10, C11: 47uF; C0805
C18, C19, C20, C21, C23, C24, C25, C26, C27: 100pF; C0402K
C22: 100pF; C0402
CR1: B560C-13-FSMC_DIO-L; SMC_DIO-L
DISPLAY: CONN_08"; 1X08
DRV_X: TMC2209_BTT_BLANK; MODULE_TMC2209_BTT_BLANK
DRV_Y: TMC2209_BTT_BLANK; MODULE_TMC2209_BTT_BLANK
DRV_Z: TMC2209_BTT_BLANK; MODULE_TMC2209_BTT_BLANK
G1: 455-1750-1-ND; 1X03
HX1, HX2: CONN_08"; 1X08
HY1, HY2: CONN_08"; 1X08
HZ1, HZ2: CONN_08"; 1X08
J5: CONN_10"; 1X10
L1: 10uH; MWSA0503S-100MT
R1, R2, R6, R7, R9, R10, R11, R12, R13, R14, R27: 10k; RESC1608X60
R3: 0R; RESC1608X60
R4, R5, R15, R16, R17, R18, R20, R21, R22: 100R; RESC1608X60
R8: 1k; RESC1608X60
R23: 100k; RESC1005X40
R24: 13k; RESC1608X60
R25: 51k; RESC1608X60
R26: 270k; RESC1005X40
S1: ENCODER-SWITCH; ROTARY_ENC_PLAIN
SEN0, SEN1, SEN2, SEN3: BM08B-GHS-TBT(LF)(SN)(N); JST_BM08B-GHS-TBT(LF)(SN)(N)
SEN0-S, SEN1-S, SEN2-S, SEN3-S: CONN_08"; 1X08
T1, T2, T3, T4, T5, T6: CONN_24; 1X24
TEENSY4: TEENSY_EXTENDED_BLANK
U1: TPS54360DDARDDA8_3P1X2P4_TEX; DDA8_3P1X2P4_TEX
V5: 455-1750-1-ND; 1X03
X_OUT: HX25418-4A
Y_OUT: HX25418-4A
Z_OUT: HX25418-4A

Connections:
+3V3: C14.1, C15.1, C16.1, C17.1, DISPLAY.1, HX1.2, HY1.2, HY2.2, HZ1.2, HZ2.3, R1.2, R2.2, R6.2, R7.2, R9.2, R10.1, R11.1, R12.1, R13.1, R14.1, R27.2, SEN0.1, SEN0-S.1, SEN1.1, SEN1-S.1, SEN2.1, SEN2-S.1, SEN3.1, SEN3-S.1, T1.22, T2.15, T3.15, T4.15, T5.22, T6.22
+5V: 5V_IN.2, C10.1, C11.1, C12.+, L1.2, R26.2, T1.24, T5.24, T6.24, V5.1, V5.2, V5.3
+24V: 24V_IN.2, C1.+, C2.+, C5.1, C6.1, C13.+, HX1.8, HY1.8, HZ1.8, U1.2 (VIN)
BL: DISPLAY.8, T2.16, T3.16, T4.16
BUTT_ENC: R6.1, S1.SW+, T2.6, T3.6, T4.6
BUTT_HAND_L: J5.1, R27.1, T2.4, T3.4, T4.4
BUTT_HAND_R: J5.3, R7.1, T2.5, T3.5, T4.5
CS0: C21.2, R12.2, R15.1, SEN0.8, SEN0-S.8
CS0_M: R15.2, T2.22, T3.22, T4.22
CS1: C22.2, R10.2, R16.1, SEN1.8, SEN1-S.8
CS1_M: R16.2, T2.12, T3.12, T4.12
CS2: C23.2, R13.2, R17.1, SEN2.8, SEN2-S.8
CS2_M: R17.2, T2.23, T3.23, T4.23
CS3: C24.2, R11.2, R18.1, SEN3.8, SEN3-S.8
CS3_M: R18.2, T2.24, T3.24, T4.24
CS4: C27.2, DISPLAY.5, R14.2, R22.1
CS4_M: R22.2, T2.21, T3.21, T4.21
DC: DISPLAY.6, T2.20, T3.20, T4.20
DIR_X: HX2.8, T1.16, T5.16, T6.16
DIR_Y: HY2.8, T1.6, T5.6, T6.6
DIR_Z: HZ2.8, T1.4, T5.4, T6.4
ENCA: S1.A, T1.19, T5.19, T6.19
ENCB: S1.B, T1.20, T5.20, T6.20
EN_X: HX2.1, T1.21, T5.21, T6.21
EN_Y: HY2.1, T1.13, T5.13, T6.13
EN_Z: HZ2.1, T1.9, T5.9, T6.9
GND: 5V_IN.1, 24V_IN.1, C1.-, C2.-, C3.2, C4.2, C5.2, C6.2, C7.2, C8.2, C10.2, C11.2, C12.-, C13.-, C14.2, C15.2, C16.2, C17.2, C18.1, C19.1, C20.1, C21.1, C22.1, C23.1, C24.1, C25.1, C26.1, C27.1, C28.2, CR1.2, DISPLAY.2, G1.1, G1.2, G1.3, HX1.1, HX1.7, HX2.2, HX2.3, HY1.1, HY1.7, HY2.3, HZ1.1, HZ1.7, HZ2.2, J5.2, J5.4, J5.6, J5.8, J5.10, R23.1, R25.1, S1.C, S1.SW-, SEN0.3, SEN0.5, SEN0.7, SEN0.P1 (SHIELD), SEN0.P2 (SHIELD), SEN0-S.3, SEN0-S.5, SEN0-S.7, SEN1.3, SEN1.5, SEN1.7, SEN1.P1 (SHIELD), SEN1.P2 (SHIELD), SEN1-S.3, SEN1-S.5, SEN1-S.7, SEN2.3, SEN2.5, SEN2.7, SEN2.P1 (SHIELD), SEN2.P2 (SHIELD), SEN2-S.3, SEN2-S.5, SEN2-S.7, SEN3.3, SEN3.5, SEN3.7, SEN3.P1 (SHIELD), SEN3.P2 (SHIELD), SEN3-S.3, SEN3-S.5, SEN3-S.7, T1.10, T1.23, T2.1, T3.1, T4.1, T5.10, T5.23, T6.10, T6.23, U1.7 (GND), U1.EPAD
LIM_X: C3.1, J5.5, R2.1, T2.7, T3.7, T4.7
LIM_Y: C4.1, J5.7, R1.1, T2.8, T3.8, T4.8
LIM_Z: C28.1, J5.9, R9.1, T2.9, T3.9, T4.9
MISO: C18.2, R3.1, SEN0.6, SEN0-S.6, SEN1.6, SEN1-S.6, SEN2.6, SEN2-S.6, SEN3.6, SEN3-S.6
MISO_M: R3.2, T2.14, T3.14, T4.14
MOSI: C19.2, R4.1, SEN0.4, SEN0-S.4, SEN1.4, SEN1-S.4, SEN2.4, SEN2-S.4, SEN3.4, SEN3-S.4
MOSI1: C25.2, DISPLAY.3, R20.1
MOSI1_M: R20.2, T2.18, T3.18, T4.18
MOSI_M: R4.2, T2.13, T3.13, T4.13
unnamed: T2.2, T3.2, T4.2
unnamed: T2.3, T3.3, T4.3
unnamed: T2.10, T3.10, T4.10
unnamed: T2.11, T3.11, T4.11
unnamed: R23.2, U1.4 (RT/CLK)
unnamed: T1.12, T5.12, T6.12
unnamed: C7.1, R24.1
unnamed: T1.3, T5.3, T6.3
unnamed: HZ1.6, Z_OUT.4
unnamed: T1.2, T5.2, T6.2
unnamed: C8.1, R24.2, U1.6 (COMP)
unnamed: HZ1.5, Z_OUT.3
unnamed: T1.8, T5.8, T6.8
unnamed: HX1.6, X_OUT.4
unnamed: HX1.5, X_OUT.3
unnamed: R25.2, R26.1, U1.5 (FB)
unnamed: HZ1.4, Z_OUT.2
unnamed: HZ1.3, Z_OUT.1
unnamed: T1.18, T5.18, T6.18
unnamed: HY1.4, Y_OUT.2
unnamed: HX1.4, X_OUT.2
unnamed: HX1.3, X_OUT.1
unnamed: T1.5, T5.5, T6.5
unnamed: R8.1, T1.15, T5.15, T6.15
unnamed: HY1.3, Y_OUT.1
unnamed: C9.2, CR1.1, L1.1, U1.8 (SW)
unnamed: C9.1, U1.1 (BOOT)
unnamed: HY1.6, Y_OUT.4
unnamed: HY1.5, Y_OUT.3
RST: DISPLAY.7, T2.17, T3.17, T4.17
RX_X: HX2.4, HY2.4, HZ2.4, R8.2, T1.14, T5.14, T6.14
SCK: C20.2, R5.1, SEN0.2, SEN0-S.2, SEN1.2, SEN1-S.2, SEN2.2, SEN2-S.2, SEN3.2, SEN3-S.2
SCK1: C26.2, DISPLAY.4, R21.1
SCK1_M: R21.2, T2.19, T3.19, T4.19
SCK_M: R5.2, T1.11, T5.11, T6.11
STP_X: HX2.7, T1.17, T5.17, T6.17
STP_Y: HY2.7, T1.7, T5.7, T6.7
STP_Z: HZ2.7, T1.1, T5.1, T6.1

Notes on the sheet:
Jumpers
Peripherals
Steppers
Sensors
Power
Buttons


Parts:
5V_IN, 24V_IN: CONN_025MM; SCREWTERMINAL-5MM-2
C1, C2, C12, C13: 100uF/50V; PANASONIC_D
C3, C4, C28: 100nF; CAPC1608X85
C5, C6: 2.2uF; CAPC1608X85
C7: 6.8nF; CAPC1608X85
C8: 39pF; CAPC1005X60
C9, C14, C15, C16, C17: 100nF; CAPC1005X60
C10, C11: 47uF; CAPC2012X110
C18, C19, C20, C21, C22, C23, C24, C25, C26, C27: 100pF; CAPC1005X60
CR1: B560C-13-FSMC_DIO-L; SMC_DIO-L
DISPLAY: CONN_08"; 1X08
DRV_X: TMC2209_BTT_BLANK; MODULE_TMC2209_BTT_BLANK
DRV_Y: TMC2209_BTT_BLANK; MODULE_TMC2209_BTT_BLANK
DRV_Z: TMC2209_BTT_BLANK; MODULE_TMC2209_BTT_BLANK
G1: 455-1750-1-ND; 1X03
HX1, HX2: CONN_08"; 1X08
HY1, HY2: CONN_08"; 1X08
HZ1, HZ2: CONN_08"; 1X08
J5: CONN_10"; 1X10
L1: 10uH; MWSA0503S-100MT
R1, R2, R6, R7, R9, R10, R11, R12, R13, R14, R27: 10k; RESC1608X60
R3: 0R; RESC1608X60
R4, R5, R15, R16, R17, R18, R20, R21, R22: 100R; RESC1608X60
R8: 1k; RESC1608X60
R23: 100k; RESC1005X40
R24: 13k; RESC1608X60
R25: 51k; RESC1608X60
R26: 270k; RESC1005X40
S1: ENCODER-SWITCH; ROTARY_ENC_PLAIN
SEN0, SEN1, SEN2, SEN3: BM08B-GHS-TBT(LF)(SN)(N); JST_BM08B-GHS-TBT(LF)(SN)(N)
SEN0-S, SEN1-S, SEN2-S, SEN3-S: CONN_08"; 1X08
T1, T2, T3, T4, T5, T6: CONN_24; 1X24
TEENSY4: TEENSY_EXTENDED_BLANK
U1: TPS54360DDARDDA8_3P1X2P4_TEX; DDA8_3P1X2P4_TEX
V5: 455-1750-1-ND; 1X03
X_OUT: HX25418-4A
Y_OUT: HX25418-4A
Z_OUT: HX25418-4A

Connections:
+3V3: C14.1, C15.1, C16.1, C17.1, DISPLAY.1, HX1.2, HY1.2, HY2.2, HZ1.2, HZ2.3, R1.2, R2.2, R6.2, R7.2, R9.2, R10.1, R11.1, R12.1, R13.1, R14.1, R27.2, SEN0.1, SEN0-S.1, SEN1.1, SEN1-S.1, SEN2.1, SEN2-S.1, SEN3.1, SEN3-S.1, T1.22, T2.15, T3.15, T4.15, T5.22, T6.22
+5V: 5V_IN.2, C10.1, C11.1, C12.+, L1.2, R26.2, T1.24, T5.24, T6.24, V5.1, V5.2, V5.3
+24V: 24V_IN.2, C1.+, C2.+, C5.1, C6.1, C13.+, HX1.8, HY1.8, HZ1.8, U1.2 (VIN)
BL: DISPLAY.8, T2.16, T3.16, T4.16
BUTT_ENC: R6.1, S1.SW+, T2.6, T3.6, T4.6
BUTT_HAND_L: J5.1, R27.1, T2.4, T3.4, T4.4
BUTT_HAND_R: J5.3, R7.1, T2.5, T3.5, T4.5
CS0: C21.2, R12.2, R15.1, SEN0.8, SEN0-S.8
CS0_M: R15.2, T2.22, T3.22, T4.22
CS1: C22.2, R10.2, R16.1, SEN1.8, SEN1-S.8
CS1_M: R16.2, T2.12, T3.12, T4.12
CS2: C23.2, R13.2, R17.1, SEN2.8, SEN2-S.8
CS2_M: R17.2, T2.23, T3.23, T4.23
CS3: C24.2, R11.2, R18.1, SEN3.8, SEN3-S.8
CS3_M: R18.2, T2.24, T3.24, T4.24
CS4: C27.2, DISPLAY.5, R14.2, R22.1
CS4_M: R22.2, T2.21, T3.21, T4.21
DC: DISPLAY.6, T2.20, T3.20, T4.20
DIR_X: HX2.8, T1.16, T5.16, T6.16
DIR_Y: HY2.8, T1.6, T5.6, T6.6
DIR_Z: HZ2.8, T1.4, T5.4, T6.4
ENCA: S1.A, T1.19, T5.19, T6.19
ENCB: S1.B, T1.20, T5.20, T6.20
EN_X: HX2.1, T1.21, T5.21, T6.21
EN_Y: HY2.1, T1.13, T5.13, T6.13
EN_Z: HZ2.1, T1.9, T5.9, T6.9
GND: 5V_IN.1, 24V_IN.1, C1.-, C2.-, C3.2, C4.2, C5.2, C6.2, C7.2, C8.2, C10.2, C11.2, C12.-, C13.-, C14.2, C15.2, C16.2, C17.2, C18.1, C19.1, C20.1, C21.1, C22.1, C23.1, C24.1, C25.1, C26.1, C27.1, C28.2, CR1.2, DISPLAY.2, G1.1, G1.2, G1.3, HX1.1, HX1.7, HX2.2, HX2.3, HY1.1, HY1.7, HY2.3, HZ1.1, HZ1.7, HZ2.2, J5.2, J5.4, J5.6, J5.8, J5.10, R23.1, R25.1, S1.C, S1.SW-, SEN0.3, SEN0.5, SEN0.7, SEN0.P1 (SHIELD), SEN0.P2 (SHIELD), SEN0-S.3, SEN0-S.5, SEN0-S.7, SEN1.3, SEN1.5, SEN1.7, SEN1.P1 (SHIELD), SEN1.P2 (SHIELD), SEN1-S.3, SEN1-S.5, SEN1-S.7, SEN2.3, SEN2.5, SEN2.7, SEN2.P1 (SHIELD), SEN2.P2 (SHIELD), SEN2-S.3, SEN2-S.5, SEN2-S.7, SEN3.3, SEN3.5, SEN3.7, SEN3.P1 (SHIELD), SEN3.P2 (SHIELD), SEN3-S.3, SEN3-S.5, SEN3-S.7, T1.10, T1.23, T2.1, T3.1, T4.1, T5.10, T5.23, T6.10, T6.23, U1.7 (GND), U1.EPAD
LIM_X: C3.1, J5.5, R2.1, T2.7, T3.7, T4.7
LIM_Y: C4.1, J5.7, R1.1, T2.8, T3.8, T4.8
LIM_Z: C28.1, J5.9, R9.1, T2.9, T3.9, T4.9
MISO: C18.2, R3.1, SEN0.6, SEN0-S.6, SEN1.6, SEN1-S.6, SEN2.6, SEN2-S.6, SEN3.6, SEN3-S.6
MISO_M: R3.2, T2.14, T3.14, T4.14
MOSI: C19.2, R4.1, SEN0.4, SEN0-S.4, SEN1.4, SEN1-S.4, SEN2.4, SEN2-S.4, SEN3.4, SEN3-S.4
MOSI1: C25.2, DISPLAY.3, R20.1
MOSI1_M: R20.2, T2.18, T3.18, T4.18
MOSI_M: R4.2, T2.13, T3.13, T4.13
unnamed: T2.2, T3.2, T4.2
unnamed: T2.3, T3.3, T4.3
unnamed: T2.10, T3.10, T4.10
unnamed: T2.11, T3.11, T4.11
unnamed: R23.2, U1.4 (RT/CLK)
unnamed: T1.12, T5.12, T6.12
unnamed: C7.1, R24.1
unnamed: T1.3, T5.3, T6.3
unnamed: HZ1.6, Z_OUT.4
unnamed: T1.2, T5.2, T6.2
unnamed: C8.1, R24.2, U1.6 (COMP)
unnamed: HZ1.5, Z_OUT.3
unnamed: T1.8, T5.8, T6.8
unnamed: HX1.6, X_OUT.4
unnamed: HX1.5, X_OUT.3
unnamed: R25.2, R26.1, U1.5 (FB)
unnamed: HZ1.4, Z_OUT.2
unnamed: HZ1.3, Z_OUT.1
unnamed: T1.18, T5.18, T6.18
unnamed: HY1.4, Y_OUT.2
unnamed: HX1.4, X_OUT.2
unnamed: HX1.3, X_OUT.1
unnamed: T1.5, T5.5, T6.5
unnamed: R8.1, T1.15, T5.15, T6.15
unnamed: HY1.3, Y_OUT.1
unnamed: C9.2, CR1.1, L1.1, U1.8 (SW)
unnamed: C9.1, U1.1 (BOOT)
unnamed: HY1.6, Y_OUT.4
unnamed: HY1.5, Y_OUT.3
RST: DISPLAY.7, T2.17, T3.17, T4.17
RX_X: HX2.4, HY2.4, HZ2.4, R8.2, T1.14, T5.14, T6.14
SCK: C20.2, R5.1, SEN0.2, SEN0-S.2, SEN1.2, SEN1-S.2, SEN2.2, SEN2-S.2, SEN3.2, SEN3-S.2
SCK1: C26.2, DISPLAY.4, R21.1
SCK1_M: R21.2, T2.19, T3.19, T4.19
SCK_M: R5.2, T1.11, T5.11, T6.11
STP_X: HX2.7, T1.17, T5.17, T6.17
STP_Y: HY2.7, T1.7, T5.7, T6.7
STP_Z: HZ2.7, T1.1, T5.1, T6.1

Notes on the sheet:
Jumpers
Peripherals
Steppers
Sensors
Power
Buttons

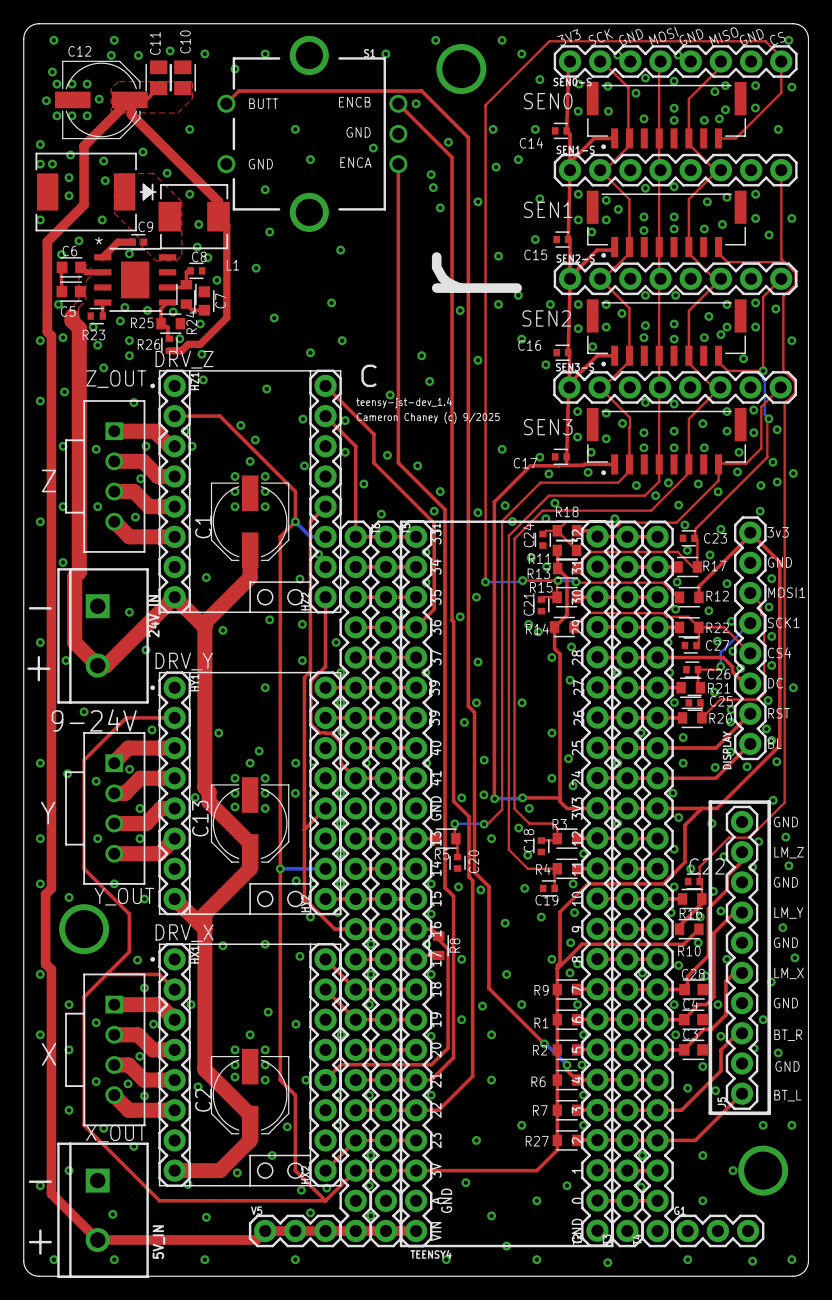
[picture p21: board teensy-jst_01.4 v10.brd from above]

Board: 2 copper layers, 66.0 x 105.4 mm, 91 parts (0 on the bottom side), 74 nets.

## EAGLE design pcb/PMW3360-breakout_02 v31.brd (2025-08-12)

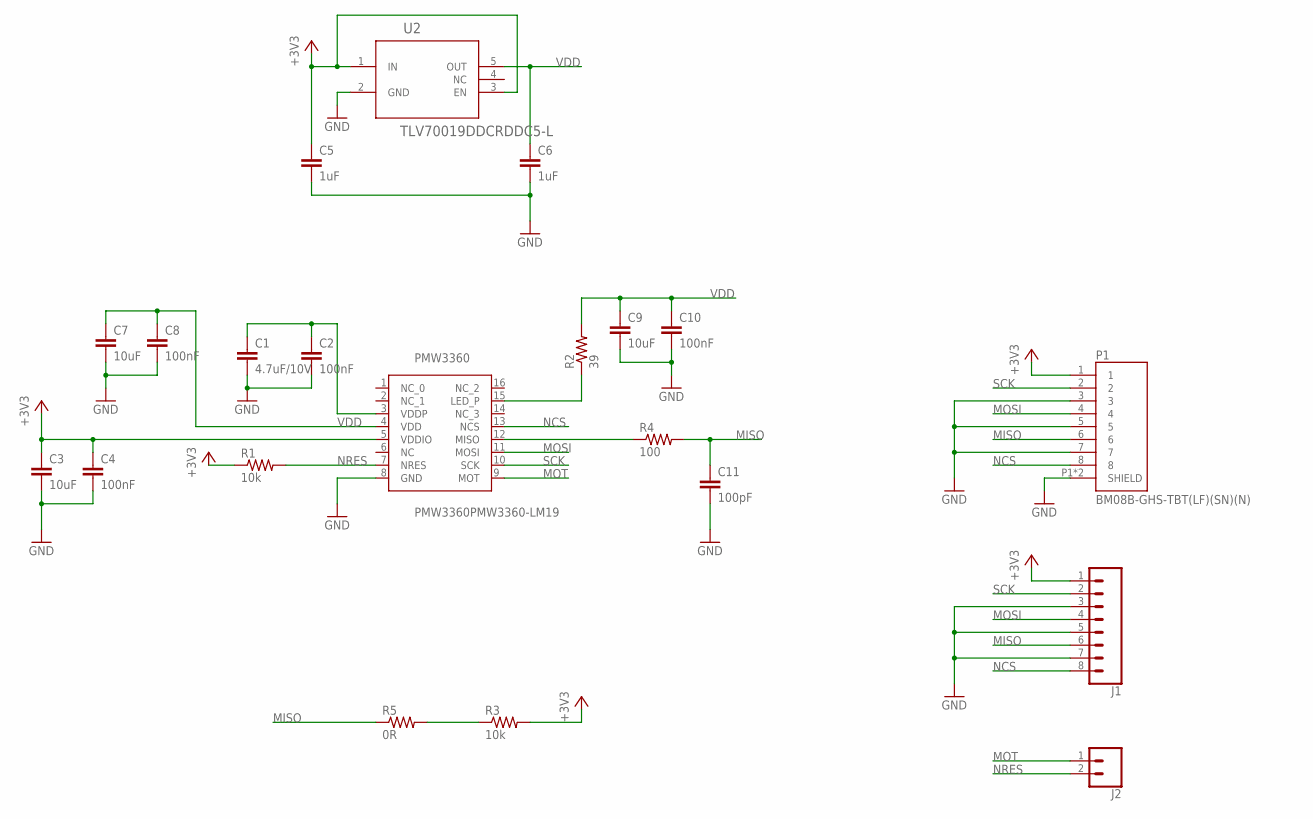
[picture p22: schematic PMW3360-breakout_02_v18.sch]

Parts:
C1: 4.7uF/10V; CAPC1608X85
C2, C4, C8, C10: 100nF; CAPC1005X60
C3, C7, C9: 10uF; CAPC1005X60
C5, C6: 1uF; CAPC1005X60
C11: 100pF; C0402K
J1: CONN_08"; 1X08
J2: CONN_02; 1X02
P1: BM08B-GHS-TBT(LF)(SN)(N); JST_BM08B-GHS-TBT(LF)(SN)(N)
PMW3360: PMW3360PMW3360-LM19; PMW3360
R1, R3: 10k; R0402
R2: 39; R0402
R4: 100; R0402
R5: 0R; R0402
U2: TLV70019DDCRDDC5-L; DDC5-L

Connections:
+3V3: C3.1, C4.1, C5.1, J1.1, P1.1, PMW3360.5 (VDDIO), R1.1, R3.2, U2.1 (IN), U2.3 (EN)
GND: C1.2, C2.2, C3.2, C4.2, C5.2, C6.2, C7.2, C8.2, C9.2, C10.2, C11.2, J1.3, J1.5, J1.7, P1.3, P1.5, P1.7, P1.P1 (SHIELD), P1.P2 (SHIELD), PMW3360.8 (GND), U2.2 (GND)
MISO: C11.1, J1.6, P1.6, R4.2, R5.1
MOSI: J1.4, P1.4, PMW3360.11 (MOSI)
MOT: J2.1, PMW3360.9 (MOT)
unnamed: PMW3360.15 (LED_P), R2.1
unnamed: C1.1, C2.1, PMW3360.3 (VDDP)
unnamed: PMW3360.12 (MISO), R4.1
unnamed: R3.1, R5.2
NCS: J1.8, P1.8, PMW3360.13 (NCS)
NRES: J2.2, PMW3360.7 (NRES), R1.2
SCK: J1.2, P1.2, PMW3360.10 (SCK)
VDD: C6.1, C7.1, C8.1, C9.1, C10.1, PMW3360.4 (VDD), R2.2, U2.5 (OUT)

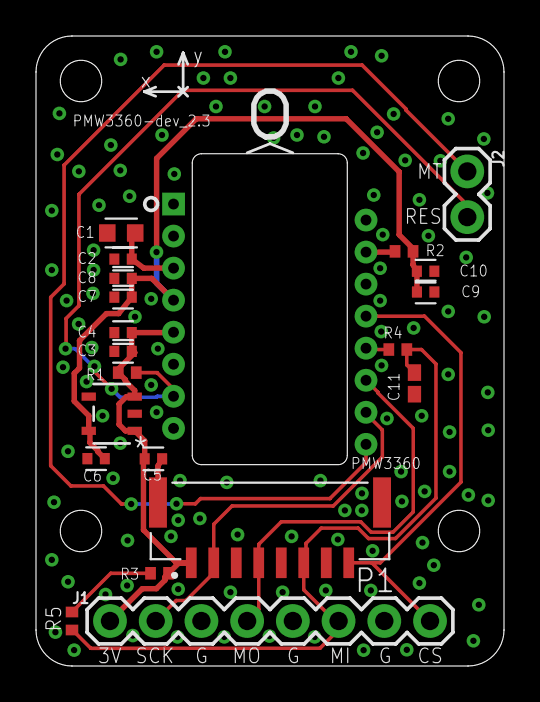
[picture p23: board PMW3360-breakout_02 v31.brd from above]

Board: 2 copper layers, 26.0 x 35.0 mm, 21 parts (0 on the bottom side), 13 nets.

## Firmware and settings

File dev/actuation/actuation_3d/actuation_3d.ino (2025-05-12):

#include <AccelStepper.h>
#include <TMCStepper.h>
// #include <PMW3360.h>
#include <SdFat.h>
#include <Arduino_GFX_Library.h>
#include <EncoderButton.h>

// Pin definitions
#define SS0   				30
#define SS1					10
#define SS2					31
#define SS3					32
#define LIMIT_MACH_X0       6
#define LIMIT_MACH_Z0       5
#define BUTT_HANDLE_L       2
#define BUTT_HANDLE_R       3
#define ENCODER_PIN_A       22
#define ENCODER_PIN_B       21
#define ENCODER_BUTT	  	4
#define MOT_EN_R    		23
#define MOT_DIR_R   		18
#define MOT_STEP_R  		19
#define MOT_EN_L    		15
#define MOT_DIR_L   		38
#define MOT_STEP_L  		39
#define MOT_EN_Z    		41
#define MOT_DIR_Z   		36
#define MOT_STEP_Z  		33
#define TFT_CS      		29
#define TFT_DC      		28
#define TFT_RST     		25
#define TFT_BL				24

// Driver settings
#define DRIVER_ADDRESS_R	0b00
#define DRIVER_ADDRESS_L  	0b01
#define DRIVER_ADDRESS_Z	0b10
#define R_SENSE            	0.11f
#define SERIAL_PORT     	Serial4
#define motorInterfaceType 	1

// Motor properties
const int stepsPerRev = 200;					// steps per revolution
const int uSteps = 4;							// microstep configuration
// A and B Motors (belt)
const float beltPitch = 2.0;					// belt pitch (mm)
const int pulleyTeeth = 16;						// pulley teeth on drive pulley
const float ConvBelt = (stepsPerRev*uSteps)/(beltPitch*pulleyTeeth);	// conversion factor (mm -> steps)
const float maxSpeedAB = 140.0*ConvBelt;			// max velocity A and B motors can move at (step/s)
const float maxAccelAB = 2000.0*ConvBelt;			// A/B motor max acceleration (step/s^2)
// Z Motor (lead screw)
const float lead = 8;							// lead screw lead (mm)
const float Conv = (stepsPerRev*uSteps)/lead;	// conversion factor (mm -> steps)
const float stepPulseWidth = 20.0;				// min pulse width (from Mark Rober's code)
const float maxCurrent_RMS = 1273.0;			// motor RMS current rating (mA)
const float maxSpeedZ = 180.0*Conv;				// max velocity Z motor can move at (step/s)
const float maxAccelZ = 3000.0*Conv;			// z max acceleration (step/s^2)
const float retract = 5;						// distance to retract (mm)
const float zeroSpeed_0 = 20.0 * Conv;			// zeroing speed (step/s)
const float zeroSpeed_1 = 4.0 * Conv;			// secondary zeroing speed (step/s)
const float zeroAccel = 200.0 * Conv;			// zeroing acceleration (step/s^2)
const float holeFeedrate = 5.0*Conv; 			// default hole feedrate (step/s)		TODO: make this modifiable

// Gantry geometry
const float xRange = 20.0;						// usable range of x-axis (mm)
const float yRange = 20.0;						// usable range of y-axis (mm)
const float zRange = 34.0;						// usable length of z-axis (mm)
const float xLimitOffset = 2.54;				// distance from wall of stepper when zeroed (mm)
const float zLimitOffset = 2.13;				// distance from wall when zeroed (mm)
const float wallBuffer = 3.0;						// safety buffer between tool body and walls (mm)

class Position {
public:
	Position(float x = 0.0f, float y = 0.0f, float z = 0.0f) : x(x), y(y), z(z) {
		clamp();
	}

	void set(float newX, float newY, float newZ) {
		x = newX;
		y = newY;
		z = newZ;
		clamp();
	}

	void setX(float newX) {
		x = newX;
		clamp();
	}

	void setY(float newY) {
		y = newY;
		clamp();
	}

	void setZ(float newZ) {
		z = newZ;
		clamp();
	}

	float getX() const { return x; }
	float getY() const { return y; }
	float getZ() const { return z; }

private:
	float x, y, z;

	void clamp() {
		x = constrainValue(x, -xRange / 2, xRange / 2);
		y = constrainValue(y, -yRange / 2, yRange / 2);
		z = constrainValue(z, 0, zRange);
	}

	float constrainValue(float value, float min, float max) {
		if (value < min) return min;
		if (value > max) return max;
		return value;
	}
};

// TODO: add a new Actuator object that initializes with motor type (lead or belt) and coreXY consideration
AccelStepper stepperR(motorInterfaceType, R, MOT_DIR_R);
AccelStepper stepperL(motorInterfaceType, MOT_STEP_L, MOT_DIR_L);
AccelStepper stepperZ(motorInterfaceType, MOT_STEP_Z, MOT_DIR_Z);
TMC2209Stepper driverR(&SERIAL_PORT, R_SENSE, DRIVER_ADDRESS_R);
TMC2209Stepper driverL(&SERIAL_PORT, R_SENSE, DRIVER_ADDRESS_L);
TMC2209Stepper driverZ(&SERIAL_PORT, R_SENSE, DRIVER_ADDRESS_Z);
EncoderButton encoder(ENCODER_PIN_A, ENCODER_PIN_B, ENCODER_BUTT);
Position desPos;

void motorSetup() {
	// Set up motors
	pinMode(MOT_EN_R, OUTPUT);
	pinMode(MOT_EN_L, OUTPUT);
	pinMode(MOT_EN_Z, OUTPUT);

	// Enable motors
	digitalWrite(MOT_EN_R, LOW);
	digitalWrite(MOT_EN_L, LOW);
	digitalWrite(MOT_EN_Z, LOW);

	delay(100);
	disableStepperZ();

	// Set motor properties
	stepperR.setMinPulseWidth(stepPulseWidth);
	stepperR.setMaxSpeed(zeroSpeed_0);
	stepperR.setAcceleration(zeroAccel);
	stepperR.setCurrentPosition(0);

	stepperL.setMinPulseWidth(stepPulseWidth);
	stepperL.setMaxSpeed(zeroSpeed_0);
	stepperL.setAcceleration(zeroAccel);
	stepperL.setCurrentPosition(0);

	stepperZ.setMinPulseWidth(stepPulseWidth);
	stepperZ.setMaxSpeed(zeroSpeed_0);
	stepperZ.setAcceleration(zeroAccel);
	stepperZ.setCurrentPosition(0);
}

void driverSetup() {
	SERIAL_PORT.begin(115200);
	delay(100);

	driverR.begin(); driverR.toff(5);
	driverL.begin(); driverL.toff(5);
	driverZ.begin(); driverZ.toff(5);

	driverR.rms_current(maxCurrent_RMS);
	driverL.rms_current(maxCurrent_RMS);
	driverZ.rms_current(maxCurrent_RMS);
	
	driverR.microsteps(uSteps);
	driverL.microsteps(uSteps);
	driverZ.microsteps(uSteps);

	driverR.pwm_autoscale(true);
	driverR.en_spreadCycle(false);
	driverR.TPWMTHRS(0x753);

	driverL.pwm_autoscale(true);
	driverL.en_spreadCycle(false);
	driverL.TPWMTHRS(0x753);
	
	driverZ.pwm_autoscale(true);
	driverZ.en_spreadCycle(false);
	driverZ.TPWMTHRS(0x753);
}

void enableStepperZ() {
	digitalWrite(MOT_EN_Z, LOW);
}

void disableStepperZ() {
	digitalWrite(MOT_EN_Z, HIGH);
}

void actuate(Position pos) {
	// actuate coreXY system
	float a = pos.getX() + pos.getY();
	float b = pos.getX() - pos.getY();
	stepperR.moveTo(a * ConvBelt);
	stepperL.moveTo(b * ConvBelt);
	stepperZ.moveTo(pos.getZ() * Conv);
}

void setup() {
	Serial.begin(115200);
	delay(100);

	// Set up systems
	motorSetup(); 
	driverSetup();

	stepperR.setMaxSpeed(maxSpeedAB);
	stepperL.setMaxSpeed(maxSpeedAB);
}

void loop() {
	if (Serial.available()) {
		char ch = Serial.read();
		switch (ch) {
			case '0':
				desPos.set(0.0f, 0.0f, 0.0f);
				break;
			case 'a':
				// move -x
				desPos.setX(desPos.getX() - 1.0f);
				break;
			case 'd':
				// move +x
				desPos.setX(desPos.getX() + 1.0f);
				break;
			case 's':
				// move -y
				desPos.setY(desPos.getY() - 1.0f);
				break;
			case 'w':
				// move +y
				desPos.setY(desPos.getY() + 1.0f);
				break;
		}
	}

	// Actuate system
	actuate(desPos);
	stepperR.run();
	stepperL.run();
	stepperZ.run();
}

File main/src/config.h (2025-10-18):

#ifndef CONFIG_H
#define CONFIG_H

#include <Arduino.h>

// Pin definitions
#define SS0   				30
#define SS1					10
#define SS2					31
#define SS3					32
#define LIMIT_MACH_X0       5
#define LIMIT_MACH_Y0		6
#define LIMIT_MACH_Z0       7
#define BUTT_HANDLE_L       2
#define BUTT_HANDLE_R       3
#define ENCODER_PIN_A       22
#define ENCODER_PIN_B       21
#define ENCODER_BUTT	  	4
#define MOT_EN_L    		23
#define MOT_DIR_L   		18
#define MOT_STEP_L  		19
#define MOT_EN_R    		15
#define MOT_DIR_R   		38
#define MOT_STEP_R  		39
#define MOT_EN_Z    		41
#define MOT_DIR_Z   		36
#define MOT_STEP_Z  		33
#define TFT_CS      		29
#define TFT_DC      		28
#define TFT_RST     		25
#define TFT_BL				24

// Driver settings
#define DRIVER_ADDRESS_L	0b00
#define DRIVER_ADDRESS_R  	0b01
#define DRIVER_ADDRESS_Z	0b10
#define R_SENSE            	0.11f
#define SERIAL_PORT     	Serial4
#define motorInterfaceType 	1

// Constants
// #define MAX_PATHS  			10
#define MAX_POINTS 			8000
#define MAX_FILES			100
#define GC9A01A_WEBWORK_GREEN 0x8FF1

// Sensor properties
const int ns = 4;								// number of sensors
const int CPI = 2500;							// counts per inch. This value changes calibration coefficients
const float lx = 120.0f;						// x length of rectangular sensor configuration (mm)
const float ly = 140.0f;						// y length of rectangular sensor configuration (mm)
const float xSensorOffset = -2.32;				
const float ySensorOffset = -3.2;				// offset to try to counteract weird rotation behavior (mm) (UNUSED)
const float driftRate = 0.001;					// drift rate of positioning (unitless, drift per distance traveled - measured)
const float maxDrift = 1;						// maximum acceptable drift (mm)

// Motor properties
const int stepsPerRev = 200;					// steps per revolution
const int uSteps = 4;							// microstep configuration
// A and B Motors (belt)
const float beltPitch = 2.0;					// belt pitch (mm)
const int pulleyTeeth = 16;						// pulley teeth on drive pulley
const float ConvBelt = (stepsPerRev*uSteps)/(beltPitch*pulleyTeeth);	// conversion factor (mm -> steps)
// Z Motor (lead screw)
const float lead = 8;							// lead screw lead (mm)
const float ConvLead = (stepsPerRev*uSteps)/lead;	// conversion factor (mm -> steps)
// Other motor properties
const float stepPulseWidth = 20.0;				// min pulse width (from Mark Rober's code)
const float maxCurrent_RMS = 1273.0;			// motor RMS current rating (mA)
const float maxSpeedAB = 140.0*ConvBelt;			// max velocity A and B motors can move at (step/s)
const float maxAccelAB = 2000.0*ConvBelt;			// A/B motor max acceleration (step/s^2)
const float maxSpeedZ = 180.0*ConvLead;				// max velocity Z motor can move at (step/s)
const float maxAccelZ = 3000.0*ConvLead;			// z max acceleration (step/s^2)
const float retract = 2.0;						// distance to retract (mm)
const float zeroSpeed_0 = 20.0;					// zeroing speed (mm/s)
const float zeroSpeed_1 = 4.0;					// secondary zeroing speed (mm/s)
const float zeroAccel = 200.0;					// zeroing acceleration (mm/s^2)
const float feedrate_default = 5.0;				// default feedrate (mm/s)
const float plungeRate_default = 5.0;			// default plunge rate (mm/s)

// Material properties
const float maxThickness = 15.0;				// upper bound of thickness knob (mm)
const float restHeight = 2.0;					// rest height of tool before cutting (mm)
const float holeTolerance = 0.25;					// tolerance for hole positioning (mm)

// Gantry geometry
const float xRange = 20.0;						// usable range of x-axis (mm)
const float xRangeHard = 24.0;					// hard limit of x-axis (mm)
const float yRange = 20.0;						// usable range of y-axis (mm)
const float yRangeHard = 24.0;					// hard limit of y-axis (mm)
const float zRange = 34.0;						// usable length of z-axis (mm)
const float zRangeHard = 34.0;					// hard limit of z-axis (mm)
const float xLimitOffset = 1.32;				// distance from wall of stepper when zeroed (mm)
const float yLimitOffset = 1.48;				// distance from wall of stepper when zeroed (mm)
const float zLimitOffset = 2.29;				// distance from wall when zeroed (mm)
const float wallBuffer = 3.0;						// safety buffer between tool body and walls (mm)

// Timing constants
const long unsigned debounceDelay = 50;			// the debounce time; increase if the output flickers
const long unsigned dtDebug = 500;				// (ms)
const long unsigned dtStopwatch = 500;			// time interval for loop timing (ms)
const long unsigned dtPlot = 50;				// (ms)
const long unsigned dtOutput = 20;				// (ms)
const long unsigned dtOutputSD = 10;			// time interval for auxiliary SD logging (ms)
const long unsigned dt = 900;					// length of sensor timestep (us)(freq = 1,000,000/timestepPoll [Hz])
const long unsigned dtControl = 500;			// length of control timestep (us)(freq = 1,000,000/timestepControl [Hz])

// UI Features (runtime configurable - defined in globals.cpp)

#endif

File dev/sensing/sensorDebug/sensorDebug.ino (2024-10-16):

// Libraries to include
#include <PMW3360_router.h>
#include <SPI.h>
#include <SD.h>
#include <EEPROM.h>
#include <EncoderButton.h>

// Function definitions
// Setup functions
void sensorSetup();
void wait_for_movement();
// Math functions
int16_t convTwosComp(int16_t value);
float mapF(long x, float in_min, float in_max, float out_min, float out_max);
float meanArray(float* arr, int size);
// Sensing functions
void sensorPlotting();
void debugging();
void doSensing();
// Other loop functions
void writeToEEPROM();
void eepromWrite(int address, float value);
float eepromRead(int address);
void onClickReset(EncoderButton &eb);

// Pin definitions -------------------------------------------------------------------------------
// Sensor pins
#define SS0   39   // Chip select pin. Connect this to SS on the module.
// #define SS1   10
// #define SS2   40
// #define SS3   32
#define SS1   9       // *** changed when soldering *** TODO: change back once ready
#define SS2   32      // *** swapped when soldering *** TODO: swap back once ready
#define SS3   40      // *** swapped when soldering *** TODO: swap back once ready
// int sensorPins[3] = {SS0, SS1, SS2};
int sensorPins[4] = {SS0, SS1, SS2, SS3};
#define ENCODER_PIN_A       21
#define ENCODER_PIN_B       22
#define ENCODER_BUTTON_PIN  4

// Constants ------------------------------------------------------------------------
// Modes
int plotting = 1;             // plot values  (1 = yes; 0 = no)
int debugMode = 0;            // print values (1 = yes; 0 = no)

// Timing properties
long unsigned debounceDelay = 50;      // the debounce time; increase if the output flickers
long unsigned dtDebug = 500;            // [ms]
long unsigned dtPlot = 50;              // [ms]
long unsigned dtStop = 2000;            // time to indicate a stop [ms]

// Sensor properties
const int ns = 4;                   // number of sensors
const int CPI = 2500;               // This value changes calibration coefficients
long unsigned dt = 500;       // microseconds (freq = 1,000,000/timestepPoll [Hz])

// Variables ------------------------------------------------------------------------
// Timing variables
int firstPoint = 1;
long unsigned timeLastPoll = 0;
long unsigned timeLastDebug = 0;
long unsigned timeLastPlot = 0;

// Measured quantities
float measVel[2][4] = {{0.0f,0.0f,0.0f,0.0f},
                      {0.0f,0.0f,0.0f,0.0f}};     // BFF (x,y) velocity of each sensor (mm/us)
float estPos[2][4] = {{0.0f,0.0f,0.0f,0.0f},
                      {0.0f,0.0f,0.0f,0.0f}}; 
byte surfaceQuality[4] = {0,0,0,0};

// Calibration variables
int sensorSelect = -1;
float cVal[2][4];            // calibration coefficient to be calculated
int axis = 0;                 // axis to calibrate (0 = x; 1 = y)

// Object Initialization ------------------------------------------------------------
// Sensor object creation
PMW3360 sensors[4];

EncoderButton encoder(ENCODER_PIN_A, ENCODER_PIN_B, ENCODER_BUTTON_PIN);

void onClickReset(EncoderButton &eb) {
  for (int i = 0; i < 4; i++) {
    estPos[0][i] = 0.0f;
    estPos[1][i] = 0.0f;
  }
}

// -------------------------------------------------------------------------------------------------
// Setup and Main Loop -----------------------------------------------------------------------------
void setup() {
  Serial.begin(115200);

  while(!Serial);         // we actually want to make sure serial is opened for calibration
  delay(100);

  Serial.println("Serial set up!");

  // Setup systems
  sensorSetup();
  encoder.setClickHandler(onClickReset);

  Serial.println("Debug ready!");
  
  delay(500);
}

void loop() {
  encoder.update();

  // Serial Interface -----------------------------------------------------------------------------
  // Serial.println("in loop");
  if (Serial.available()) {
    char ch = Serial.read();
    if (ch == '0') {
      for (int i = 0; i < 4; i++) {
        estPos[0][i] = 0.0f;
        estPos[1][i] = 0.0f;
      }
    }
  }

  // if (sensorSelect != -1) {
  doSensing();
  // }

  debugging();
}

// ------------------------------------------------------------------------------------------------
// Setup subfunctions -----------------------------------------------------------------------------
void sensorSetup() {
  // Sensor initialization
  for (int i = 0; i < 4; i++) {
    if (sensors[i].begin(sensorPins[i], CPI, SPI)) {
      Serial.print("Sensor");
      Serial.print(i);
      Serial.print(" initialization succeeded, with CPI = ");
      Serial.println(sensors[i].getCPI());
    } else {
      Serial.print("Sensor");
      Serial.print(i);
      Serial.println(" initialization failed");
    }
  }
}

// Loop subfunctions -----------------------------------------------------------------------------
// Math functions
int16_t convTwosComp(int16_t value){
  // Convert from 2's complement (16 bit now)
  // This is needed to convert the binary values from the sensor library to decimal

  if (value & 0x8000) {                     // Check if the sign bit is set (negative value)
    return -((~value & 0xFFFF) + 1);      // Invert bits, add one, make negative
  } else {
    return value;
  }
}

// Sensing functions
void doSensing() {
  if(micros() - timeLastPoll >= dt) {
    timeLastPoll = micros();

    // Sensing ---------------------------------------------------------------------
    // Collect sensor data (raw)
 
    PMW3360_DATA data[4];
    for (int i = 0; i < 4; i++) {
      data[i] = sensors[i].readBurst();
      surfaceQuality[i] = data[i].SQUAL;
    }

    for (int i = 0; i < 4; i++) {
      // Sensor velocity sensing
      // measVel[0][i] = -convTwosComp(data[i].dx);     // '-' convention is used to flip sensor's z axis
      measVel[0][i] = convTwosComp(data[i].dx);
      measVel[1][i] = convTwosComp(data[i].dy);

      // Integrate linear velocities to get position
      estPos[0][i] = estPos[0][i] + measVel[0][i];
      estPos[1][i] = estPos[1][i] + measVel[1][i];
    }

    // Sensor plotting
    sensorPlotting();
  }
}

void sensorPlotting() {
  // Plot sensor data
  if(millis() - timeLastPlot >= dtPlot && plotting) {
    timeLastPlot = millis();

    for (int i = 0; i < 4; i++) {
      // Serial.printf("x_%i:%f,y_%i:%f",i,estPos[0][i],i,estPos[1][i]);
      Serial.printf("sq_%i:%d",i,surfaceQuality[i]);
      Serial.println();
    }
    // Serial.printf("x_raw:%f,y_raw:%f",measVel[0][sensorSelect],measVel[1][sensorSelect]);
    // Serial.printf("dx:%i,dy:%i",data.dx,data.dy);
    // Serial.printf("x:%f,y:%f",estPos[0][sensorSelect],estPos[1][sensorSelect]);
    //    Serial.printf("w1:%f,w2:%f,w3:%f,w4:%f,w5:%f,w6:%f,w7:%f,w8:%f",estAngVel[0],estAngVel[1],
    //      estAngVel[2],estAngVel[3],estAngVel[4],estAngVel[5],estAngVel[6],estAngVel[7]);
    // Serial.printf("x:%f,y:%f",xmm[1],ymm[1]);
    Serial.println();
  }
}
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

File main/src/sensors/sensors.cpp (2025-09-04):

#include "sensors.h"

/*
Sensor configuration:
0 --- 1    ^ y
|  x  |    |-> x
2 --- 3

Angle signage: +CCW
*/

// Timing variables
static long unsigned timeLastPlot = 0;

// Additional tracking variables
static int surfaceQuality[4] = {0,0,0,0};
static bool onSurface[4] = {1,1,1,1};		// 1 if sensor is on surface, 0 otherwise
static float estVel[2][4] = {{0.0f,0.0f,0.0f,0.0f},
							{0.0f,0.0f,0.0f,0.0f}};
static float estAngVel[8] = {0.0f,0.0f,0.0f,0.0f,0.0f,0.0f};

void sensorSetup() {
	int sensorPins[4] = {SS0, SS1, SS2, SS3};

	screen->fillScreen(BLACK);
	int size = 2;
	int16_t centerX = screen->width() / 2;
	int16_t centerY = screen->height() / 2;
	int16_t totalHeight = 4 * size * 10;			// 4 lines, size 2, 10px per line
	int16_t yStart = centerY - totalHeight / 2;
	int16_t x1, y1;
	uint16_t w, h;
	char text[10];

	sprintf(text, "v%s", FIRMWARE_VERSION);
	screen->getTextBounds(text, 0, 0, &x1, &y1, &w, &h);
	int16_t xStart = centerX - w / 2;
	screen->setCursor(xStart, yStart - size *10);
	screen->println(text);

	for (int i = 0; i < 4; i++) {
		// display each sensors' initialization status on the screen, showing each sensor on a new line
		// and setting text color green or red depending on initialization status
		Serial.print("Sensor");
		Serial.print(i);

		if (sensors[i].begin(sensorPins[i], CPI)) {
			screen->setTextColor(GREEN);

			Serial.print(" initialization succeeded, with CPI = ");
			Serial.println(sensors[i].getCPI());
		} else {
			screen->setTextColor(RED);

			Serial.println(" initialization failed");
		}

		sprintf(text, "Sensor %i", i);
		screen->getTextBounds(text, 0, 0, &x1, &y1, &w, &h);
		xStart = centerX - w / 2;
		screen->setCursor(xStart, yStart + i * size * 10);
		screen->println(text);
	}
}

int16_t convTwosComp(int16_t value) {
	if (value & 0x8000) {
		return -((~value & 0xFFFF) + 1);
	} else {
		return value;
	}
}

void doSensing() {
	// TODO: fix how sensingTime is implemented. Currently, on the first iteration, sensingTime
	// 	is incredibly large because timeLastPoll is either 0 or set from a while ago. This usually
	// 	isn't a huge issue because the router starts from rest, but there are certain cases where
	//  this isn't true.
	sensingTime = micros() - timeLastPoll;
	timeLastPoll = micros();
	unsigned long logTime = filemicros;

	// Collect sensor data
	PMW3360_DATA data[ns];
	SensorData logData[ns];
	for (int i = 0; i < ns; i++) {
		data[i] = sensors[i].readBurst();
	}

	// Process sensor data
	for (int i = 0; i < ns; i++) {
		float dx = -convTwosComp(data[i].dx);
		float dy = convTwosComp(data[i].dy);
		surfaceQuality[i] = data[i].SQUAL;
		onSurface[i] = data[i].isOnSurface;
		
		// TODO: find better way to check for bad readings. surfaceQuality does not seem to be reliable
		if (onSurface[i]) {
			float sinfr = sinf(cal[i].r);
			float cosfr = cosf(cal[i].r);
			measVel[0][i] = cal[i].x * (dx*cosfr - dy*sinfr) / sensingTime;
			measVel[1][i] = cal[i].y * (dx*sinfr + dy*cosfr) / sensingTime;
		} else {
			// TODO: why are we evaluating the sensor validity below instead of here?
			measVel[0][i] = NAN;
			measVel[1][i] = NAN;
			// Serial.printf("Sensor %i is not on surface\n", i);
		}

		// Store sensor data for logging
		// TODO: store the raw int and byte data instead and do twosComp in the decoder
		logData[i].dx = dx;
		logData[i].dy = dy;
		logData[i].onSurface = data[i].isOnSurface;
		logData[i].sq = data[i].SQUAL;
		logData[i].rawDataSum = data[i].rawDataSum;
	}

	// Calculate angular velocities
	estAngVel[0] = (measVel[0][2] - measVel[0][0])/ly;
	estAngVel[1] = (measVel[0][2] - measVel[0][1])/ly;
	estAngVel[2] = (measVel[0][3] - measVel[0][0])/ly;
	estAngVel[3] = (measVel[0][3] - measVel[0][1])/ly;
	estAngVel[4] = (measVel[1][1] - measVel[1][0])/lx;
	estAngVel[5] = (measVel[1][1] - measVel[1][2])/lx;
	estAngVel[6] = (measVel[1][3] - measVel[1][0])/lx;
	estAngVel[7] = (measVel[1][3] - measVel[1][2])/lx;

	// Average angular velocities
	float sumAngVel = 0.0f;
	float estAngVel1 = 0.0f;
	int num_good_calcs = 0;				// number of measurements that are valid
	for (int i = 0; i < 8; i++) {
		// filter out bad measurements
		if (!isnan(estAngVel[i])) {
			sumAngVel = sumAngVel + estAngVel[i];
			num_good_calcs++;
		}
	}

	if (num_good_calcs == 0) {
		valid_sensors = false;
		return;
	} else {
		valid_sensors = true;
		estAngVel1 = sumAngVel / num_good_calcs;
	}

	// Body position estimation
	// TODO: turn this into "matrix" math
	float sinfy = sinf(pose.yaw);
	float cosfy = cosf(pose.yaw);
	estVel[0][0] = measVel[0][0]*cosfy-measVel[1][0]*sinfy + 0.5*estAngVel1*(lx*cosfy-(ly)*sinfy);
	estVel[0][1] = measVel[0][1]*cosfy-measVel[1][1]*sinfy + 0.5*estAngVel1*(lx*cosfy+(ly)*sinfy);
	estVel[0][2] = measVel[0][2]*cosfy-measVel[1][2]*sinfy + 0.5*estAngVel1*(-lx*cosfy-(ly)*sinfy);
	estVel[0][3] = measVel[0][3]*cosfy-measVel[1][3]*sinfy + 0.5*estAngVel1*(-lx*cosfy+(ly)*sinfy);
	estVel[1][0] = measVel[0][0]*sinfy+measVel[1][0]*cosfy + 0.5*estAngVel1*((ly)*cosfy+lx*sinfy);
	estVel[1][1] = measVel[0][1]*sinfy+measVel[1][1]*cosfy + 0.5*estAngVel1*(-(ly)*cosfy+lx*sinfy);
	estVel[1][2] = measVel[0][2]*sinfy+measVel[1][2]*cosfy + 0.5*estAngVel1*((ly)*cosfy-lx*sinfy);
	estVel[1][3] = measVel[0][3]*sinfy+measVel[1][3]*cosfy + 0.5*estAngVel1*(-(ly)*cosfy-lx*sinfy);

	// Simple average of linear velocities
	float sumVelX = 0.0f;
	float sumVelY = 0.0f;
	float estVel1[2] = {0.0f, 0.0f};
	num_good_calcs = 0;
	for (int i = 0; i<ns; i++) {
		// filter out bad measurements
		if (!isnan(estVel[0][i]) && !isnan(estVel[1][i])) {
			sumVelX = sumVelX + estVel[0][i];
			sumVelY = sumVelY + estVel[1][i];
			num_good_calcs++;
		}
	}
	if (num_good_calcs == 0) {
		// TODO: make this prompt a re-zeroing
		// Serial.print("Sensors are poo-poo!");
		valid_sensors = false;
		return;
	} else {
		valid_sensors = true;
		// (TODO: figure out deeper cause) Acounting for weird rotation
		// estVel1[0] = (sumVelX / ns) - estAngVel1*(xSensorOffset*sinf(pose.yaw) + ySensorOffset*cosf(pose.yaw));
		// estVel1[1] = (sumVelY / ns) + estAngVel1*(xSensorOffset*cosf(pose.yaw) - ySensorOffset*sinf(pose.yaw));
		estVel1[0] = sumVelX / num_good_calcs;
		estVel1[1] = sumVelY / num_good_calcs;
	}

	// Integrate to get position and orientation
	pose.yaw = pose.yaw + estAngVel1*sensingTime;
	pose.x = pose.x + estVel1[0]*sensingTime;
	pose.y = pose.y + estVel1[1]*sensingTime;

	float distRatio = 0.6f;
	dXY = distRatio*dXY + (1-distRatio)*sqrtf(estVel1[0]*estVel1[0] + estVel1[1]*estVel1[1]) * sensingTime;
	distanceTraveled += dXY;
	// Serial.printf("distanceTraveled: %.2f\n", distanceTraveled);

	if (sensingTime > 1000 || sensingTime < 800) {
		Serial.printf("%lu: sensing time = %lu\n", millis(), sensingTime);
	}
	// Write to SD card
	if (outputSDOn) {
		writeSensorData(logTime, logData, sensingTime);
	}
}
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

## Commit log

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2023-02-24 adding datasheet and cad stuff
    [ADNS-2610_frame.stl, mousefinal.dxf]
2023-03-06 adding files and changing for esp32
    [ADNS-2610_frame_01.stl, ADNS-2610_frame_02.stl, ADNS-2610_frame_03.stl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]
2023-03-09 sensor frame CAD updates
    [PMW-3360_frame.stl, PMW-3360_frame_01.stl, PMW-3360_frame_02.stl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]
2023-03-14 moving CAD
    [ADNS-2610_frame.stl, ADNS-2610_frame_01.stl, ADNS-2610_frame_02.stl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]
2023-03-19 calibration CAD files
    [PMW3360_sled_01.stl, PMW3360_sled_02.stl, calRail1.dxf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]
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2023-03-20 changing sensor indexing to 0 based
    [PMW3360_sled_03.stl, dremelMount.stl, dremelSinch.stl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]
2023-04-06 CAD and matlab
    [UIFrameLeft.stl, UIFrameRight.stl, basePlate.dxf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]
2023-04-11 CAD v3 dev
    [handleLeft.stl, handleRight.stl, penMount.stl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]
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2023-04-16 CAD dev v4
    [UIFrameLeft.stl, UIFrameRight.stl, UIPanel.dxf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]
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2023-04-19 protoboard dev
    [boardFrame.dxf]
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2023-04-28 z raising is working and wall detect added
    [pen_mount.stl, pen_mount4.stl]
2023-04-28 Limit switch failsafes
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2023-06-26 reset functionality working
    simply press x0y0 button
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2023-07-15 new designs
    [wave01.dxf]
2023-09-27 CAD update
    [UIFrameLeft.stl, UIFrameRight.stl, UIPanel2.dxf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]
2023-10-19 CAD and debugging stuff
    [pen_mount_s01.stl, pen_mount_s01_02.stl, pen_mount_s02.stl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]
2023-11-15 updated CAD
    [frameLeft.stl]
2023-11-19 deleting CAD
    [ADNS-2610_frame.stl, ADNS-2610_frame_01.stl, ADNS-2610_frame_02.stl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]
2023-12-01 more CAD
    [frameLeft.stl, pen_mount_spring.stl]
2023-12-04 adding zCarriagePlate
    [zCarriagePlate.dxf]
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2023-12-05 cleaning up CAD stuff
    [PMW-3360_frame.stl, PMW-3360_frame_01.stl, PMW-3360_frame_02.stl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]
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2023-12-05 added base.dxf file
    [base.dxf]
2024-01-17 adding sensor sled for ogen pcb
    [PMW3360-sled_ogen.stl]
2024-01-19 updating CAD for ogen and electrical
    [handleRight.stl, springMount_ogen.stl]
2024-01-25 adding sharpie mount
    [sharpie_mount_s04.stl]
2024-01-25 deleting unecessary sleds
    [PMW-3360_frame.stl, PMW-3360_frame_01.stl, PMW-3360_frame_02.stl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]
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2024-02-13 updating frameRight for rod holes
    [frameRight.stl]
2024-05-03 bringing calibration back to dev
    [vacuumMount.stl]
2024-05-03 cleaning up and moving designs to dev
    [wave01.dxf]
2024-05-07 fixing some bugs and testing
    [main.cpp]
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2024-05-12 updating for EEPROM and fixing mistake
    Realized I had a big mistake when updating the format in a recent commit (35caf797bebce27daa01360cafb4d30068f043c5) where I didn't actually apply the calibration coefficients to the sensor outputs. Fixing that and updating for using EEPROM.
    [main.cpp]
2024-05-14 fixing bugs with array formatting
    [main.cpp]
2024-05-15 add animation for logs and fix tool position bug
    [main.cpp]
2024-05-15 downsamplign outputSerial and fixing sin error
    [main.cpp]
2024-05-15 fixed that dang desiredposition equation
    [main.cpp]
2024-05-15 undo tool position fix
    [main.cpp]
2024-05-15 fixing the desiredPosition function too
    [main.cpp]
2024-06-06 motor driver fix
2024-06-06 debug central out here
    [UIPanel_screen.dxf]
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2024-06-12 fix 4 path circle generator
    [main.cpp]
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2024-06-20 jank design state drift fix
    [main.cpp]
2024-07-09 Revert "jank design state drift fix"
    This reverts commit eb99a223ee7252543f7dc20b3d2c710897c88279.
    [main.cpp]
2024-07-19 moving dev folder to main repo
    [wave01.dxf]
2024-08-02 fixing yOffset implementation
    And fixing the output serial of stepper current position to fix int type error
    [main.cpp]
2024-08-02 Started bare bones of gcode parse and processing
    [basePlate_test.csv]
2024-08-02 add header to csv
    [basePlate_test.csv]
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2024-10-03 path planning algorithm development
    [1002.csv, basePlate_test.csv, cal.csv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]
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2024-10-07 fixed gcode parser
    not perfect, but can compile now
    [main.cpp]
2024-10-15 4 sensor integration
    fixing other things too such as motor current, calibration technique (with sensorDebug), and serial commands
    [main.cpp, sensorDebug.ino, write_eeprom_calibration.ino]
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2024-10-17 some UI dev
    also increasing z speed, fixing handle buttons, and removing SETTING_THICKNESS
    [main.cpp]
2024-10-29 temp folder rename for case switch
    [PMW3360-sled_ogen.stl, PMW3360_sled_03.stl, UIFrameLeft.stl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]
2024-10-29 rename to lowercase
    [PMW3360-sled_ogen.stl, PMW3360_sled_03.stl, UIFrameLeft.stl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]
2024-10-29 reorganizing folders and removing archive
    [PMW3360-sled_ogen.stl, PMW3360_sled_03.stl, UIFrameLeft.stl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]
2024-10-29 updating readme and moving files
    [PMW3360-breakout_01 v9.csv, PMW3360-breakout_01.brd, PMW3360-breakout_01.sch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]
2024-11-05 easy solder pcb added
    [PnP_teensy-jst_01.1 v3_front.csv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]
2024-12-20 reverted button press boolean
    Combining them made it so that the buttons didn't have to be pressed
    [main.cpp]
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2024-12-24 found z bug...
    When copying code from stepper X to stepper Z in the driver setup, I forgot to change the TPWMTHRS to Z...
    [config.h, motors.cpp, speed_test_xy.ino]
2024-12-24 fixing z skip and more conservative speeds
    [accel_TMC_test.ino, config.h, motors.cpp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]
2025-01-20 fixing path generation from gcode
    [logging.cpp, path-generators.cpp, types.h]
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2025-01-22 new cad uploaded
    [PMW3360-breakout_01 v9.csv, PMW3360-breakout_01.brd, PMW3360-breakout_01.sch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]
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2025-01-22 fixed bug between hole and normal feature I think
    Just changed the advance function from a bool to a void...
    [logging.cpp, path-execution.cpp]
2025-01-23 added 3DP version of UIPanel
    [UIPanel_screen_3DP.stl, crossPanel_3DP.stl]
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2025-02-05 adding rest of CAD
    [suckMountBody_01.stl, suckMountLid_01.stl, vacBrush_01.stl]
2025-02-14 cad updates
    adding DW611 and other fixes
    [DW611_mount_bottom.stl, DW611_mount_top.stl, RT0701C_mount_bottom.stl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]
2025-02-14 changes for new pcb, and other
    Also fixing minZ bug for drawing, adding a minZ property to the path type
    [config.h, display.cpp, globals.cpp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]
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2025-02-15 adding spacer
    [spacer_enclosure.stl]
2025-02-20 adding compatibility with aliexpress display
    [UIPanel_screen_3DP.stl]
2025-02-20 fixing corrupt cad files
    [penMount_bic.stl, penMount_papermate.stl]
2025-02-20 moving tool mounts to own folder
    [DW611_mount_bottom.stl, DW611_mount_top.stl, RT0701C_mount_bottom.stl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]
2025-02-20 pen mounts for cylindrical routers added
    [penMount_pm_65.stl, penMount_pm_71.stl, penMount_pm_dremel.stl]
2025-02-25 new dremel mount
    [dremelMount_01.stl, dremelMount_02.stl]
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2025-03-17 removing while loop for plunges
    Added a drill preset design. Also fixed the bug (that I just discovered) where if the last point is (0,0) it will be skipped.
    [config.h, display.cpp, main.cpp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]
2025-03-18 adding calibration progress bar
    And converting tanf to tan2f for sensor misalignment calculation
    [sensors.cpp]
2025-03-18 adding mother enclosure
    [cableClip.stl, motherEnclosure.stl]
2025-03-27 fixes bug with triple click
    [config.h, encoder.cpp, globals.cpp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]
2025-03-27 fixed UI panel and new step
    [UIPanel_screen_3DP.stl]
2025-03-27 fixing hole bounds
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2025-04-15 closing file correctly and debugging time
    [compassDecoder.py, encoder.cpp, logging.cpp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]
2025-04-17 fixing logging time and adding hover cursor
    [compassDecoder.py, globals.cpp, logging.cpp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]
2025-04-17 add dt to logData and plot sensors in python
    also found potential bug in sensing where the first sensingTime value is always very large
    [compassDecoder.py, logging.cpp, main.cpp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]
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2025-05-12 fixed preset path generators to retract
    [path-generators.cpp]
2025-05-12 gcode parsing fixed for 3d
    [display.cpp, logging.cpp, main.cpp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]
2025-05-12 improving logging
    - added firmware version to .ini
    - added motorToCartesian function
    - fileMicros timer
    - more handleserial options
    - fixing design in a folder bug
    - add logFile dir if doesn't exist
    - switching to binary file output
    - adding packet writers
    - changing aux packet to include 3D info
    [globals.cpp, logging.cpp, main.cpp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]
2025-05-12 fixing path bug between designs
    Used to keep the last point as the goal when switching to a new design
    [path-execution.cpp, planner.cpp]
2025-05-12 fixing sine square generator
    [config.h, encoder.cpp, path-generators.cpp]
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2025-06-20 motor swap
    Swapping the L and R motor inputs to make wiring easier
    [config.h]
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2025-06-26 fixing merge bugs
    `
    [path-execution.cpp, types.h]
2025-06-26 adding 3 axis cad
    [PMW3360-sled.stl, PMW3360_sled_02.stl, UIFrameLeft_01.stl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]
2025-07-04 fixing file navigation
    using currentPath instead of just currentDir, which broke after getting 2 directories deep
    [penMount-flange_pm65.stl, penMount-flange_pm71.stl, penMount_bic.stl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]
2025-07-08 fixing datalogging for 3 axes
    [compassDecoder.py, config.h, logging.cpp]
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2025-07-10 removing old cad files
    [DW611_mount_bottom.stl, DW611_mount_top.stl, RT0701C_mount_bottom.stl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]
2025-07-19 fixing faulty sensor filtering
    Wasn't dividing by num_good_calcs! Classic
    [sensors.cpp]
2025-07-22 up to date PCB files
    [PMW3360-breakout_02 v21.brd, PMW3360-breakout_02 v21.csv, PMW3360-breakout_02 v25.csv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]
2025-07-24 updating CAD files
    updating a couple parts for 6mm basePlate, as well as updating readme
    [baseStagePlug.stl, facePlate.dxf, facePlate.step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]
2025-07-24 updating springmount and baseplate for 6mm
    [basePlate.step, baseplate.dxf, springMount.stl]
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2025-07-30 deeper countersinks for baseplate
    [basePlate.step, baseplate.dxf]
2025-08-05 updating xStagePlate for better clearance
    [xStagePlate.stl]
2025-08-10 adding beltsShim
    [beltShim.stl]
2025-08-12 PCB design files
    [PMW3360-breakout_02 v28.brd, PMW3360-breakout_02_v16.sch, teensy-jst_01.4 v9.brd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]
2025-08-12 better sensor pcb
    fixed dumb mistake
    [PMW3360-breakout_02 v25.csv, PMW3360-breakout_02 v28.brd, PMW3360-breakout_02 v31.brd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]
2025-08-16 adding sensorJig
    [sensor-jig.stl]
2025-08-18 specify stranded wires for sensor cables
    [sensor_ETH_20_CAT5.bom.tsv, sensor_ETH_40_CAT5.bom.tsv]
2025-08-21 plunge and retract speeds fixed
    [config.h, globals.cpp, motors.cpp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]
2025-08-25 teensy PCB with correct capacitor footprints
    [PnP_teensy-jst_01.4 v10_front.csv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]
2025-08-26 fixing speed update after plunge
    [motors.cpp]
2025-09-04 doesn't need M800 anymore
    [logging.cpp]
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2025-09-13 added newer fdm parts
    [displayRing_01.stl, displayRing_ae.stl, displayRing_ws.stl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]
2025-09-26 diamond display fix from opensauce
    [display.cpp]
2025-10-11 fixing nut slots and zKnob
    [baseStage.stl, frameUILeft.stl, frameUIRight.stl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]
2025-10-13 cable clearance for idler mounts
    [idlerMountLeft.stl, idlerMountLeftRight.stl]
2025-10-18 Add path preview functionality and UI enhancements
    - Introduced path preview feature in the UI, allowing users to visualize the path.
    - Added reset functionality for path preview when entering the READY state.
    - Updated display logic to draw path previews conditionally.
    - Implemented functions to clear and store path elements for efficient rendering.
    [config.h, display.cpp, encoder.cpp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]
2025-10-18 Reset path preview on file selection and add debugging output for path bounds. Gcode preview not working yet, generated preview is
    [logging.cpp]
2025-10-20 Refactor actuator update logic and fix axis inversion in UI mapping (proably only on my build) uncomment for your own build
    [display.cpp]

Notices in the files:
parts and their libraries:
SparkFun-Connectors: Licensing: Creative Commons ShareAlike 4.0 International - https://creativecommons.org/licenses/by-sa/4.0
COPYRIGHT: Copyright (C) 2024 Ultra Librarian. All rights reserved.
